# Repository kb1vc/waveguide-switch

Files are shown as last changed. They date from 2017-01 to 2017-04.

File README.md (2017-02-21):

# Description:

This is an OpenSCAD model for a positioner using a model airplane
servo to control a WR90 waveguide switch.

There are four major components in the SCAD file, each may be
printed separately.

The base holds the servo, a magnet to "capture" the positioning
slug, and two mounts for optical sensors that signal proper alignment
and positioning of the slug.

The slug connects to the shaft of the waveguide switch.  The slug
has two "vanes" that hold small magnets to latch the assembly into
the transmit or receive position.

The cap covers and protects the positioner and associated control
electronics.

For optimal performance, add a stripe of white or copper paint to
the "outside" edge of the slug vanes to provide a strong positive
reflection when the slug is in position.

---------
Arduino sketch
---------

The arduino sketch is written for the module described in the "module"
subdirectory. It is based on the Sparkfun Aruino Pro Mini. 

# License:
See the LICENSE.txt file for copyright and conditions for re-use.

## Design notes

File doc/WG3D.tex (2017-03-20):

\documentclass[12pt]{article}
% font size could be 10pt (default), 11pt or 12 pt
% paper size coulde be letterpaper (default), legalpaper, executivepaper,
% a4paper, a5paper or b5paper
% side coulde be oneside (default) or twoside 
% columns coulde be onecolumn (default) or twocolumn
% graphics coulde be final (default) or draft 
%
% titlepage coulde be notitlepage (default) or titlepage which 
% makes an extra page for title 
% 
% paper alignment coulde be portrait (default) or landscape 
%
% equations coulde be 
%   default number of the equation on the rigth and equation centered 
%   leqno number on the left and equation centered 
%   fleqn number on the right and  equation on the left side
%
\usepackage{graphicx}
\usepackage{geometry}
\usepackage{epigraph}
\usepackage{url}
\usepackage{fancybox}
\usepackage{textpos}
\usepackage{indentfirst}
\usepackage{rotating}
\usepackage{pdflscape}
\usepackage{listings}
\usepackage{tcolorbox}
\definecolor{light-gray}{gray}{0.95}
\usepackage{courier}
\usepackage{appendix}
\lstset{basicstyle=\footnotesize\ttfamily,breaklines=true,numbers=left}
%\usepackage{parskip}
%\setlength{\parskip}{\medskipamount}
\makeatletter
\newcommand{\@minipagerestore}{\setlength{\parskip}{\medskipamount}
\setlength{\parindent}{17pt}}
  \makeatother

\title{Reclaiming a Waveguide Switch -- An Adventure In 3D Printing}
\author{Matt Reilly  \\
	kb1vc \\
	}

\date{\today} 
% \date{\today} date coulde be today 
% \date{25.12.00} or be a certain date
% \date{ } or there is no date 
\begin{document}
% Hint: \title{what ever}, \author{who care} and \date{when ever} could stand 
% before or after the \begin{document} command 
% BUT the \maketitle command MUST come AFTER the \begin{document} command! 
\maketitle

\begin{abstract}
  A simple and somewhat reliable 3D printer can now be had for about \$200.
  While such a printer can help create new widgets and interesting objects, 
  it also affords an opportunity to refurbish or even reclaim equipment that
  may be lying around the shop in need of a hard-to-get part. This is the
  story of one such project that replaced a burned out actuator with a
  R/C model airplane servo and an Arduino controller.  All for 
  less than the cost of a replacement unit on eBay.
\end{abstract}

\setlength{\epigraphwidth}{0.8\textwidth}
\epigraph{[Engineering] is the art of doing that well with one dollar,
  which any bungler can do with two after a fashion.}{Arthur M. Wellington \\
  ``The Economic Theory of \\
  the Location of Railways''}

%\tableofcontents % create a table of contens 

\section{Introduction}

Most engineers read Mr. Wellington's dictum with great pride
that their training has placed them above the run-of-the-mill bungler.
I know that I do.
When it comes to mechanical engineering, however, I am a bungler.
In this case Wellington provides encouragement: it {\em may} be possible
to do what an expert can do for just twice the cost!

And so began my adventures in 3D printing.

\begin{figure}[htb]
  \centering
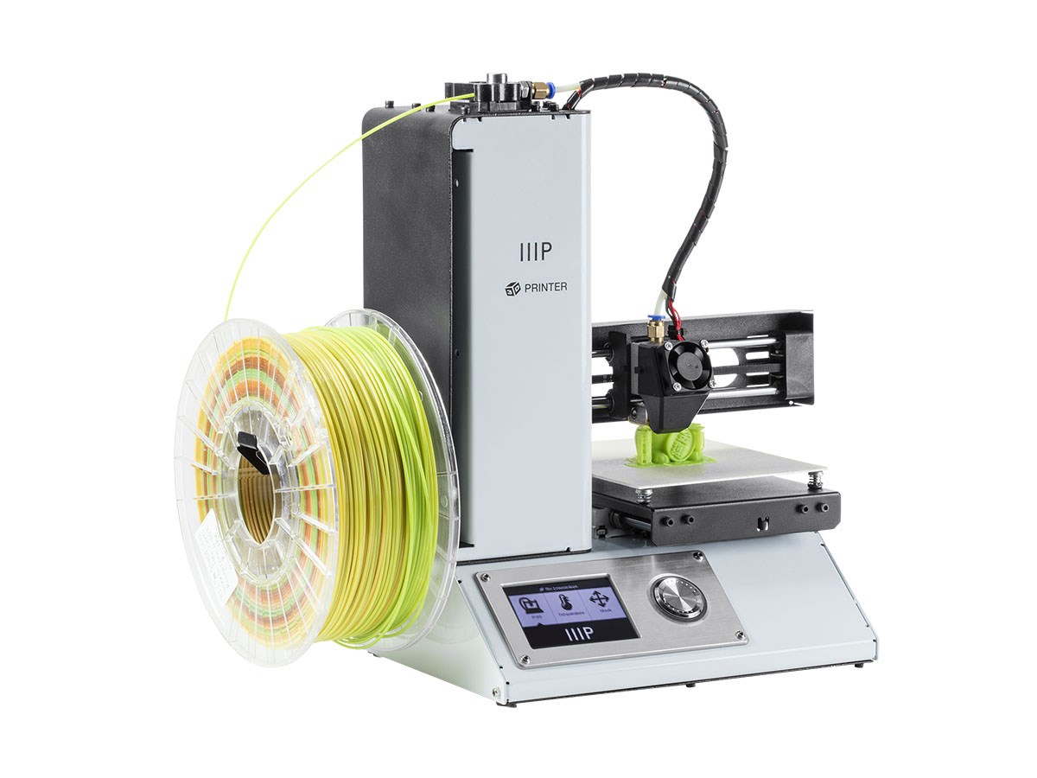
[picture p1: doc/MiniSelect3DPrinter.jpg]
  
  \caption{\label{f_printer}The Monoprice Mini Select 3D Printer}
\end{figure}

\section{Starting Simple}

This article is about reclaiming a WR75 waveguide switch by adapting
a common hobby airplane servo to function as the positioner. It comprises
a set of plastic parts to couple the servo to the waveguide slug,
and an Arduino controller.

But before we dive in to the construction of the waveguide switch positioner,
it may help to look at a much simpler 3D printing project.

Quite a while back, I bought an HP6289A DC power supply at a hamfest.
It was a real find, but at some point in its checkered past it had
been dropped on its face.  The fall shattered the two fine adjustment
knobs.  These were concentric with the coarse adjustment knobs on two
shafts: one for voltage and the second for current.  For years, the
absence of the knobs was no great annoyance. But one night I decided
that making replacements might be a short and simple project.

In the old days, I'd have scavenged in the scrap box for a nylon rod
or perhaps even an aluminum bar, mounted it in the lathe, turned it down,
bored out the hole for the shaft, tracked a few pieces of swarf while
passing through the living room, found that it didn't quite fit, tried
again... In total, I'd have spent a happy hour or two all together from
looking for bar stock, to vacuuming swarf out of the carpet.

This kind of project really points out the virtues of an inexpensive
3D printer.  No great precision is needed, and the cost of a mistake
is a small amount of material and time waiting for the
printer to finish.\footnote{The knobs were very small and simple. They
  took about 15 minutes to print. Typical
  print times for most interesting components can range from one to
  eight hours.}
It took two tries to get the design right. Had I
been paying attention, it could have been right the first time.
But having the printer in the shack
meant that I got through two iterations in less than an hour.
And no metal waste got stuck in the carpet. 

\begin{figure}[tb]
  \centering
  
  \caption{\label{f_3d_process}Printing in 3D from Idea to Widget}
\end{figure}

Figure \ref{f_3d_process} shows the path to a printed widget.  The
process starts with an idea which is reduced to a 3D model using
OpenSCAD to produce a stereo-lithography (STL) file.  The STL file
describes the object as a set of surfaces that bound a solid volume.
This is converted into instructions that move a 3D printer's extruder
and deposit the hot filament into the desired shape. The conversion
program is called a ``slicer'' because it converts the solid model
into a series of two dimensional planes that are deposited in layers
by the extruder.  The printer for this project is a Monoprice Mini
Select from \url{https://www.monoprice.com/} shown in Figure
\ref{f_printer}.The retail price is \$199. The quality of output from
the printer is variable, but compares favorably with much more
expensive printers. Though the manufacturers claim it can print in a
variety of materials, it works best with PLA, and not at all well with
ABS.

\begin{figure}[tb]
  %\caption*{About Materials}
\fbox{%
  \begin{minipage}{\textwidth}
\begin{tcolorbox}[colback=gray!35]
    \begin{center}
      {\bf About Materials}
    \end{center}
    ABS (Acrylonitrile Butadiene Styrene, for those keeping score at
    home) is the familiar plastic that shows up in instrument cases,
    helmets, canoes, and waste pipes.  It can be machined, and can
    even be given a glossy finish with exposure to acetone vapors.  It
    is, however, difficult to print on an economy-priced printer.

    PLA (Polylactic Acid) is most often found in disposable drinking
    cups.  It is often used where its potential for recycling is
    important. Some would claim that it is ``biodegradable'' as there
    are bacteria that eat it.  This has caused concern that
    widgets built with PLA might disintegrate while in use.  However,
    the process of breaking down PLA requires a fair amount of
    pressure and/or heat.  Relative durability for PLA can be assured
    by avoiding installations in compost heaps or animals.  Though my
    shack is something of a mess, it has not yet achieved the status
    of ``compost heap.''
    \end{tcolorbox}
\end{minipage}}
\end{figure}

Making the replacement knobs began with a model in OpenSCAD. OpenSCAD
scripts describe three dimensional things by building them
up from simple solids like cubes, spheres, cylinders, and cones.
Shapes can be added or subtracted, so that a simple knob can be
described as an outer cylinder minus an inner cylinder.  The inner
cylinder is the hole for the salvaged shaft collar. OpenSCAD allows the designer to
view an object on screen and to translate scripts into STL (stereo-lithography)
files for later processing. (The description language and the OpenSCAD
editor are described at \url{http://www.openscad.org/}.)

As this project aimed to replace the rather fancy HP original components,
the knobs had a bit of a taper to them, and a hole in the side for a
retaining screw. Figure \ref{f_openscad} is a screenshot of an OpenSCAD
session showing the knob. The model file is shown in Figure \ref{f_knob_list}.

\begin{figure}[htbp]
  \lstinputlisting{HP6289_inner.scad}
  \caption{\label{f_knob_list}OpenSCAD Model of Replacement Knob}
  \end{figure}

OpenSCAD scripts can follow many forms, but my own approach is to put
all of the important dimensions at the top of the file, and then
describe each feature of the object hierarchically.  For the knobs,
it was useful to describe the shaft diameter (line 2), 
the minimum wall thickness (line 3), the length of the knob (line 5),
the set screw (lines 6 and 7), and the depth of cut for the knurling (line 8).

The knob itself comprises a body, a hole for the shaft collar, a hole
for the setscrew, and the knurling.  These are all assembled in the
last module {\tt HP6289\_Inner}. The module is actually expanded in
lines 39 and 40.  OpenSCAD's default unit is the millimeter, but I
tend to measure in imperial units, so line 39 translates from inches
to mm.

\begin{figure}[tb]
  \centering
  \begin{minipage}[b]{0.4\textwidth}
    \centering
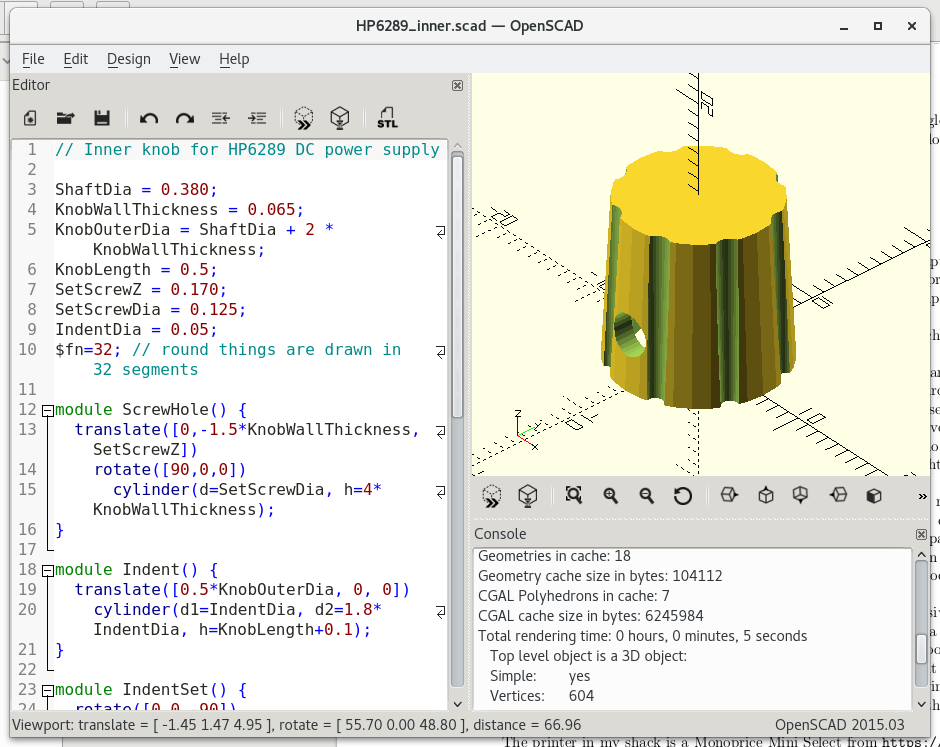
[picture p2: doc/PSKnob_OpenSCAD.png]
    
    \caption{\label{f_openscad}OpenSCAD session showing replacement knob}
  \end{minipage}\qquad
  \begin{minipage}[b]{0.4\textwidth}
    \centering
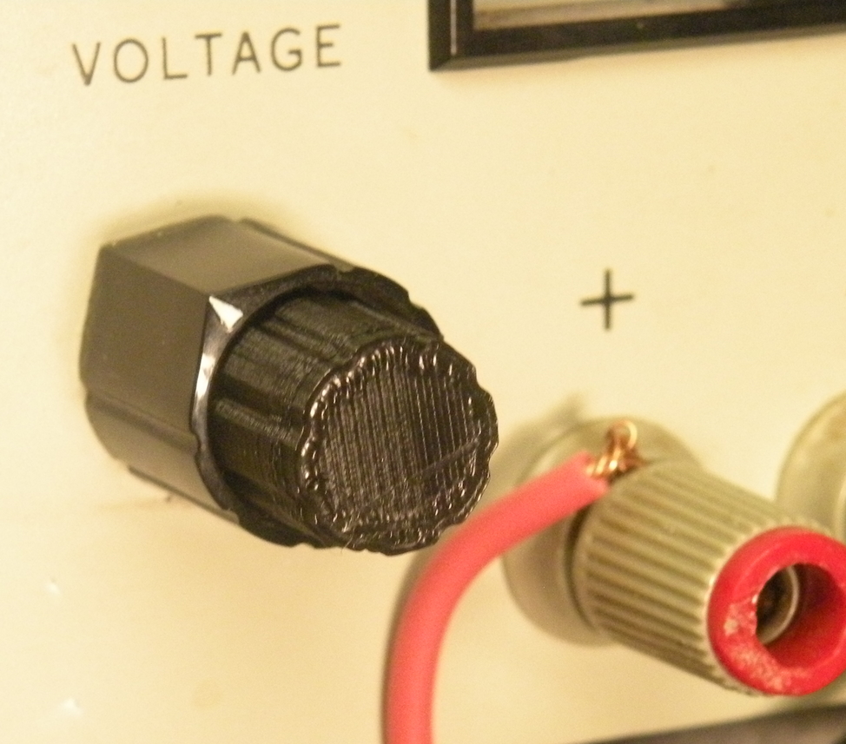
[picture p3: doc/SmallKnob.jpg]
    
    \caption{\label{f_knobs_on_box}Replacement power supply knob in its new home}
  \end{minipage}
\end{figure}

A pleasant evening of head-scratching and printing produced the two
knobs shown in Figure \ref{f_knobs_on_box}.  The result won't be
mistaken for original parts, but the power supply is a tool in a
workshop, not a museum display.

\section{The Waveguide Switch}

Years ago I bought a WR75 waveguide switch to use in a 10GHz transceiver.
The actuator was a pair of coils mounted to a shaft, and surrounded by
a pair of permanent magnets.  The shaft moved a slug inside the switch.
The switch functioned well for about ten years, but finally gasped its last
when one of the coils melted. (It appears that the microswitch that
handled the latching function may have gotten stuck.)

I disassembled the unit to complete the forensic investigation.  A short
examination convinced me that it was toast.  Rewinding the armature was
not all that appealing, and I'd recently acquired some good microwave relays,
so the broken shards sat on the shelf for a year or so, until I found the body
of the switch while looking for something else. The notion hit me that I
could replace the coil/magnet assembly with a R/C model airplane servo.
These were inexpensive and easy to control with an Arduino microcontroller
and a few lines of code.

Figure \ref{f_wg_switch_orig} shows a switch similar to the unit I started
with.\footnote{Thanks to Dudley Lab \url{http://www.dudleylab.com/surplus6.html} for the image.}  
The ``finished'' unit is shown in Figure \ref{f_wg_switch_new}. 

\begin{figure}[tb]
  \centering
  \begin{minipage}[b]{0.4\textwidth}
    \centering
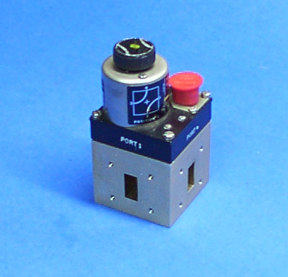
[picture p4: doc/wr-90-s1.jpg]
    
    \caption{\label{f_wg_switch_orig}Original switch (+/-)}  
  \end{minipage}
  \begin{minipage}[b]{0.4\textwidth}
    \centering
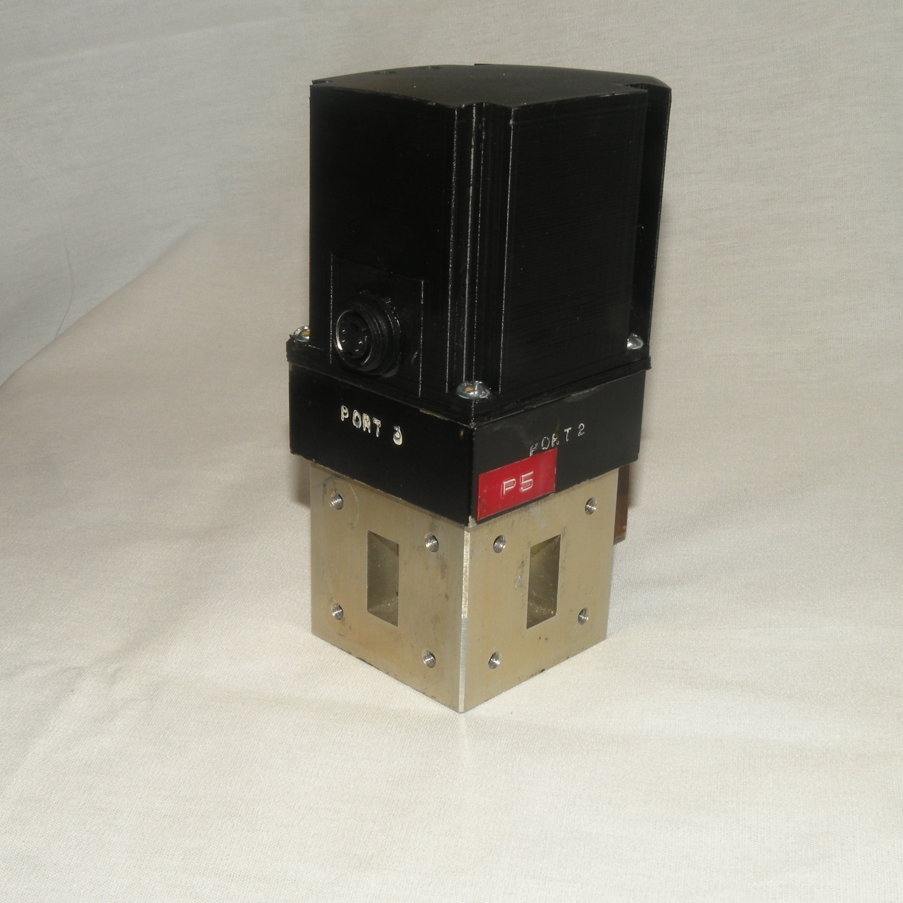
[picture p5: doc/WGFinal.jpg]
    
    \caption{\label{f_wg_switch_new}Reclaimed unit}      
  \end{minipage}
  \end{figure}

The trick was mating the servo to the keyed shaft of the waveguide switch,
and sensing the position of the switch.  A typical servo is not very
accurate. The control mechanism is a pulse train where the angular position
of the servo is more-or-less proportional to the pulse width.  The more-or-less
part meant that any positioning mechanism would need some kind of feedback
or other scheme to make sure the waveguide slug was aligned with the input
and output ports.

As an amateur bungler, it took a number of experiments before a
reasonably reliable method for positioning the slug was found. Figure
\ref{f_trial_and_error} shows 30 or so parts that were printed on the
way to a working design.  The total cost for all the material used in
the trials was less than \$10.

\begin{figure}[tb]
  \centering
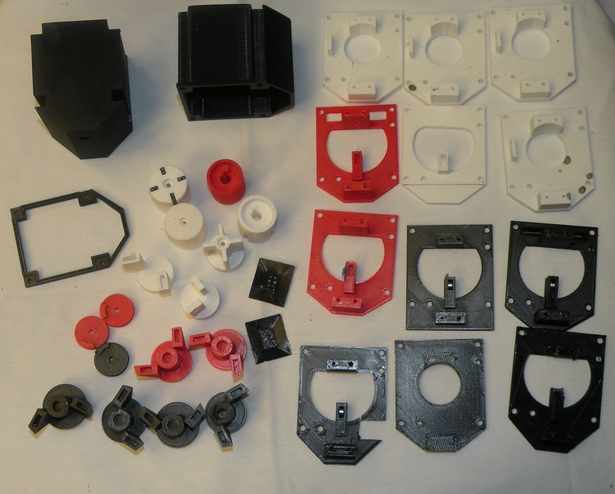
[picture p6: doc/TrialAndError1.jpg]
  
  \caption{\label{f_trial_and_error}Trial and Error Parts}
\end{figure}

\begin{figure}[thb]
\centering
    
    \caption{\label{f_expview}The Positioning Mechanism (minus the servo)}  
\end{figure}

Positional accuracy is established with a mechanical stop at each
position as shown by the assembly view in Figure \ref{f_expview}. The
metal slug in the waveguide switch itself is coupled to a positioner
(dark gray) that is pushed by the puck (white) into the RX or TX
position, and stopped by a protrusion on the base (red). Each vane in
the positioner has a pocket for a small 6mm rare earth magnet. These
are captured by a magnet in the pocket in the stop block on the
base. The servo needs only to push the positioner vane to the stop and
may then recede. The magnets hold the positioner (and the waveguide
slug) in place until the servo is commanded to switch modes.  As a
``fail-safe'' mechanism, the controller will not assert its TX\_EN
output line until an infra-red position sensor detects that the
positioner vane is in place against the stop block.  On deassertion of
the PTT line, the controller maintains the servo position against the
positioner until a similar IR sensor on the RX side detects that the
positioner is in place against the stop block on the RX side.

The servo is controlled with an Arduino Pro Mini (available from
Sparkfun at \url{https://www.sparkfun.com/products/11113}) on a module
that provides level translation and limited isolation for the PTT
input line and the TX\_EN output line. (See Appendix \ref{a_controller_module}
for the schematic.)

The OpenSCAD files, the schematic and PCB layout, and Arduino code are
all available for use under the ``BSD 2-clause Simplified License'' that
allows commercial use, modification, distribution, and private use.
The design package can be downloaded from github at \url{https://github.com/kb1vc/waveguide-switch}.

\section{Building the Switch}

It would be surprising if anyone actually built exactly this module,
as it will likely require some modification for each type of waveguide
switch.  Nevertheless, the assembly instructions are provided here to
serve as a starting point for others. Assembly directions are tedious
and make for lousy reading.  You've been warned. 

\subsection{The Arduino Controller}

The first version of the Arduino based controller assumed ground-to-actuate
input for the PTT switch that was routed directly to the microcontroller.
(See the schematic in Appendix \ref{a_controller_module}.)
This is a really bad idea, so revision B will have some protection on this
input to isolate the microcontroller from potentially damaging voltages on the
PTT line and to provide some RF decoupling.
The REV A modules are available from OSH Park at \url{https://oshpark.com/shared_projects/Da0N0VIn}.
REV B is ``in progress.''

Assembly of the controller is straightforward, though almost all the components
are surface-mounted. The Pro Mini is soldered to the module as a daughter card.
The Pro Mini is availble in both 3.3V and 5V versions.  This controller uses the
5V model, as this tends to be better suited to driving an RC servo.

Once assembled, the controlling sketch may be downloaded into the module using a
USB to serial adapter from Sparkfun. (\url{https://www.sparkfun.com/products/9716})

The sketch is found in the design package under {\tt ../arduino/TRSwitchSleep}
and its current version is shown in Appendix \ref{a_sketch}. 
This sketch senses changes on the PTT input and activates the servo.
The servo is driven to its limit until the IR sensors mounted on the base indicate
that the positioner vane is pushing against the stop block. 
The TX enable output line is asserted {\em only} after the IR sensor detects
that the positioner is in the TX position.  The TX enable line is deasserted
(floats) as soon as the microcontroller detects a rising edge on the PTT input.
The sketch places the microcontroller in sleep mode between switching events to
reduce RF noise caused by its internal (and rather dirty) oscillators. 

\subsection{The Mechanical Bits}

The 3D printed parts for the switch are all described in a single
OpenSCAD file.  However, most small 3D printers will need to print
the lid and base parts separately, as they take up a fair amount
of room on the printer's platform.
To print the components:
\begin{enumerate}
\setlength\itemsep{0em}
\item Use OpenSCAD to generate an STL file (called {\tt WGSwitch.stl}) from
  the {\tt WGSwitch.scad} source file.
\item Open the {\tt WGSwitch.stl} file in Cura
\item Click MB3 on the model and select ``Split object into parts.''
  This will separate the four parts.
\item Delete the lid and the  base.
\item Save the gcode file as {\tt WGSwitchSmall.gcode}.
\item Quit Cura, then repeat steps 2 and 3.
\item This time delete all the parts except the base.
\item Save the gcode file as {\tt WGSwitchBase.gcode}.
\item Quit Cura, then repeat steps 2 and 3.
\item Delete all the parts except the lid.
\item Flip the lid over so that its open part faces up.
\item Save the gcode file as {\tt WGSwitchLid.gcode}.
\item Copy each of the gcode files to your 3D printer.
\item For best results, print the all components in black.
  At a minimum, the positioner and the base must be printed
  in a color that does not reflect IR well.
  \end{enumerate}

It would be a very bad idea to make this your {\em first} 3D printing
experience, as every printer requires a little fiddling and some
occasional attention.  The typical 3D printer is not nearly as
reliable as a 2D inkjet printer.

\begin{figure}[tb]
  \centering
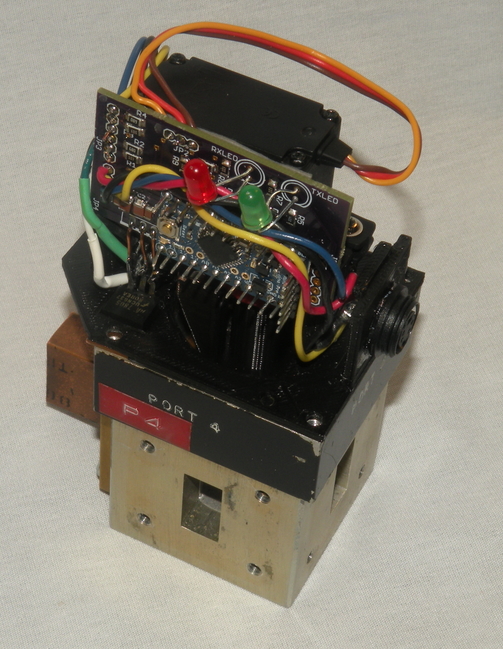
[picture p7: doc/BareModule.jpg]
  
  \caption{\label{f_naked_switch}The Controller, Servo, and Sensors}
\end{figure}

Once the parts have been printed, they should be ``tidied up'' with
a sharp knife here and there.  
The switch controller, {\em sans} lid, is shown in Figure \ref{f_naked_switch}.
Assembly is fairly straightforward.

\begin{enumerate}
\setlength\itemsep{0em}  
\item Mount the round puck on the shaft of the RC servo. Rotate the
  servo so that the shaft is at its midpoint position. Then align
  the key on the puck so that it is closest to the midpoint of the
  two mounting holes nearest the servo's shaft.
\item Mount the positioner onto the waveguide slug.
\item Insert two of the rare-earth magnets into the slots in
  the positioner, making sure the magnets are both facing with
  their poles in the same direction.
\item Place the base onto the waveguide switch body, lining up
  the locator and screw holes. Insert the LM7805 voltage regulator
  into the slot in the base. Ensure that the positioner vanes
  straddle the stop block in the base. Fasten the base to the
  switch body with four screws.
\item Insert a magnet into the slot in the base, making sure
  it is oriented so that it attracts each of the vanes in turn.
\item Glue the two IR proximity sensors into the base using
  a two-part epoxy.
\item Wire the IR sensors, the servo, and a 4 pin DIN connector
  to the controller module.
\item Fasten the controller to the side of the servo with
  double sided tape.
\item Paint a small reflective stripe on each of the vanes of the
  positioner, as shown in Figure \ref{f_positioner_stripe}.
  These will improve the reflectivity of the block. 
\item Glue the 4 pin DIN socket into the hole at one end
  of the base.
  \item Carefully stuff all that into the lid. 
  \end{enumerate}

\begin{figure}[tb]
  \centering
  
  \caption{\label{f_positioner_stripe}Reflective Stripes on the Positioner Vanes}
\end{figure}

\begin{figure}[tb]
  %\caption*{About Materials}
\fbox{%
  \begin{minipage}{1.1\textwidth}
\begin{tcolorbox}[colback=gray!35]
    \begin{center}
      {\bf Drawing in 3D}
    \end{center}
There are lots of choices for preparing 3D models
for printing.  I prefer to use open source software.
Of the open source choices, I've used two:  FreeCAD
and OpenSCAD. 

FreeCAD is an open source alternative to the traditional
3D CAD suites like SolidWorks.  The interface and
the behavior will be familiar to users of the commercial
tools.  It provides a rich set of ``workbenches'' that
assist in creating parts, assemblies, and 2D drawings.
It is under active development, and has a support community.

OpenSCAD uses a script based approach to create constructive
solid geometry  models.  It is extremely powerful, and capable
of describing just about any physically realizable shape.

I started in 3D printing as a FreeCAD user.  It allowed me to
build boxes, knobs, and robot parts. However, I found that making
changes to a design was hit-and-miss.  The data structures that
FreeCAD used often made it impossible to move a hole a few mils,
or change the angle between two slabs.  After a particularly
aggravating episode where  several hours of work had to be
discarded because a hole was in the wrong place, I abandoned FreeCAD.

OpenSCAD encourages a cut-and-try approach that allows
easy modification.  The learning curve can be quite steep for
users who have never written a program before, but not insurmountable.

A third option offers a graphical approach to constructive solid geometry. 
Many elementary schools are using Tinkercad (\url{https://www.tinkercad.com})
to introduce students to 3D printing. Tinkercad runs in a web browser, but
allows the user to create models and download them for printing on a
3D printer. 
    \end{tcolorbox}
\end{minipage}}
\end{figure}

\clearpage
\section{Final Thoughts}

The arrival on the market of
an inexpensive 3D printer, and the well established Arduino
culture have given hams a new set of tools.  Experiments are
cheap and take far less time than traditional machine-shop
ventures. The project described here was done over a few
widely spaced weekends, despite the dozens of experiments
and refinements along the way. 

Building it was fun. The trial-and-error-and-error approach
took advantage of the low cost of each print.
The CAD tools allowed progressive refinement.
The minimal investment for each design iteration meant
that ``throw it out and start over'' was always an option.
The printer produced a usable device. And the
tools are available to any bungler.

\clearpage

\begin{appendices}

\section{\label{a_sketch}The Controller Arduino Sketch}
\lstinputlisting{../arduino/TRSwitchSleep/TRSwitchSleep.ino}

\clearpage
\newgeometry{top=1cm,bottom=1cm,left=1cm,right=1cm}
\section{\label{a_controller_module}The Servo Controller Module}
\begin{figure}[h] 
  \centering
  
\end{figure} 

%%\newpage
%%\newgeometry{top=1cm,bottom=1cm,left=1cm,right=1cm}
%%\section{\label{a_controller_mdoule}The Servo Controller Module}
%%
%%\begin{landscape}
%%\includegraphics[width=0.6\linewidth,keepaspectratio]{WGSwitchSchematic.pdf}
%%  \end{landscape}
%%\restoregeometry

\end{appendices}
\end{document}

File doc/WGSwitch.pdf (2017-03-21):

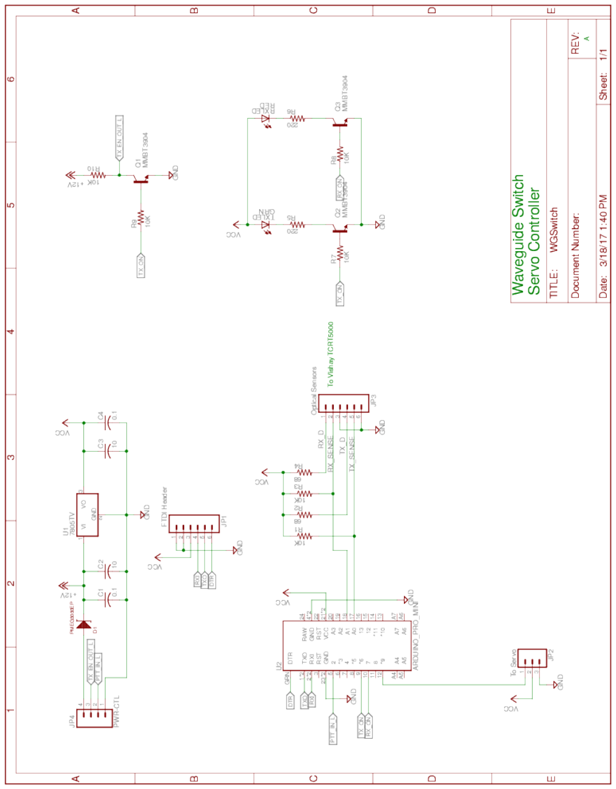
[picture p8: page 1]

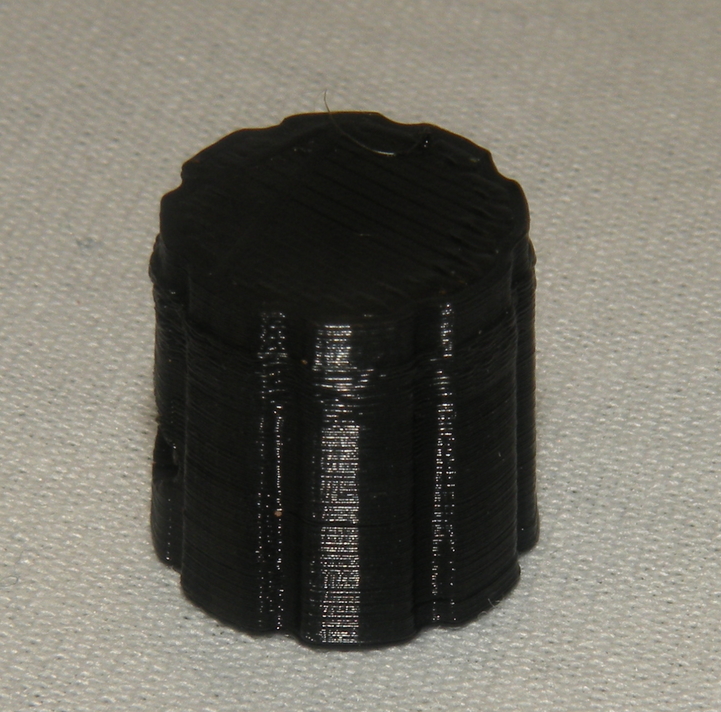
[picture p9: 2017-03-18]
doc/SmallKnobAlone.jpg

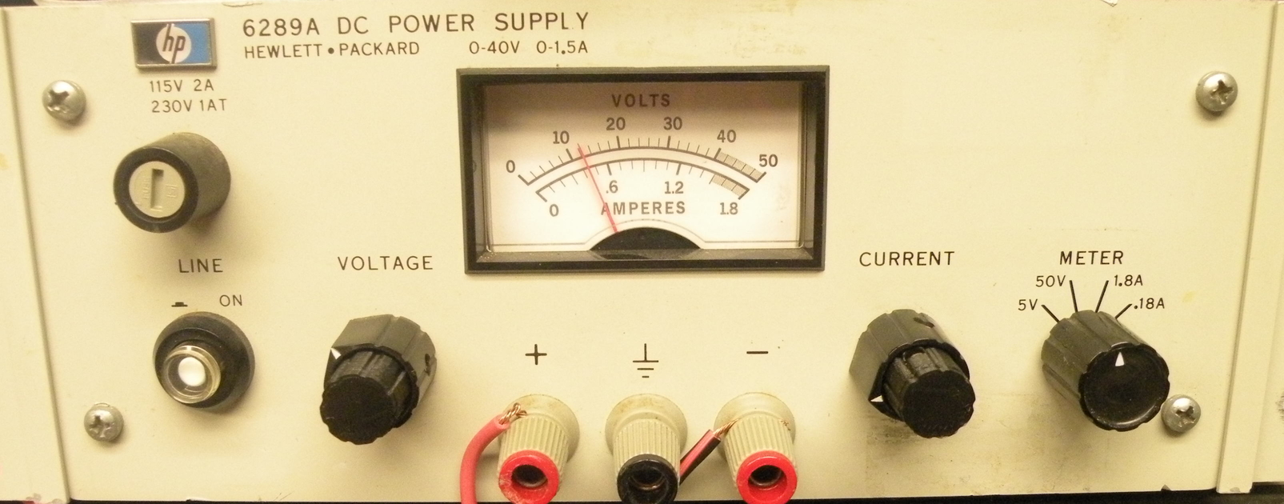
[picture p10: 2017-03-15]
doc/PSKnobs.jpg

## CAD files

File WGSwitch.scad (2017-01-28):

/*
  WGSwitch.scad
 
  Author: radiogeek381@gmail.com

 A replacement for the electro-magnetic actuated servos on a
 WR90 waveguide switch.  This uses a standard model R/C servo
 to move the slug, and permanent magnets to hold the slug in place.
*/ 
/*
Copyright (c) 2016, Matthew H. Reilly (kb1vc)
All rights reserved.

Redistribution and use in source and binary forms, with or without
modification, are permitted provided that the following conditions are
met:

    Redistributions of source code must retain the above copyright
    notice, this list of conditions and the following disclaimer.
    Redistributions in binary form must reproduce the above copyright
    notice, this list of conditions and the following disclaimer in
    the documentation and/or other materials provided with the
    distribution.

THIS SOFTWARE IS PROVIDED BY THE COPYRIGHT HOLDERS AND CONTRIBUTORS
"AS IS" AND ANY EXPRESS OR IMPLIED WARRANTIES, INCLUDING, BUT NOT
LIMITED TO, THE IMPLIED WARRANTIES OF MERCHANTABILITY AND FITNESS FOR
A PARTICULAR PURPOSE ARE DISCLAIMED. IN NO EVENT SHALL THE COPYRIGHT
HOLDER OR CONTRIBUTORS BE LIABLE FOR ANY DIRECT, INDIRECT, INCIDENTAL,
SPECIAL, EXEMPLARY, OR CONSEQUENTIAL DAMAGES (INCLUDING, BUT NOT
LIMITED TO, PROCUREMENT OF SUBSTITUTE GOODS OR SERVICES; LOSS OF USE,
DATA, OR PROFITS; OR BUSINESS INTERRUPTION) HOWEVER CAUSED AND ON ANY
THEORY OF LIABILITY, WHETHER IN CONTRACT, STRICT LIABILITY, OR TORT
(INCLUDING NEGLIGENCE OR OTHERWISE) ARISING IN ANY WAY OUT OF THE USE
OF THIS SOFTWARE, EVEN IF ADVISED OF THE POSSIBILITY OF SUCH DAMAGE.
*/

// All dimensions are in inches -- scaling to mm is at the end.

$fn=32;

// the base plate that is screwed to the top
// of the waveguide switch
BaseX = 2.6;
// for reasons I can't recall BaseX is involved in the positioning of
// the slug's magnet boxes.. go figure.
BaseXOuter = 2.8;
BaseY = 2.1;
BaseZ = 0.1;

FrameRailWidth = 0.15;

MountX = 0.22;
MountY = 0.7;
MountZ = 0.950;
// was 0.415
MountPos = [ [0.380, 0.5 * (BaseY - MountY), 0], [2.31, 0.5 * (BaseY - MountY), 0] ];

// My printer undersizes round Z axis holes by about this much.
HoleCorrection = 0.013;
// and it undersizes z axis pegs by about this much.
PegCorrection = 0.005; 

CenterHoleDia = 1.6; 
// the base is really a square with an extension off the end of the right edge.
CenterHolePos = [0.5*BaseY - 0.035, 0.5*BaseY, 0]; 

ServoCenterOffsetX = 0.540; 
ServoCenterYSpace = 0.4;
ServoCenterXSpace = 1.9; 
ServoMountHoleDia = 0.08; 
ServoMountHoleZ = MountZ * 2;
ServoMountLLHole = CenterHolePos - [ServoCenterOffsetX, 0.5 * ServoCenterYSpace, 0];
ServoMountULHole = ServoMountLLHole + [0, ServoCenterYSpace, 0];
ServoMountURHole = ServoMountULHole + [ServoCenterXSpace, 0, 0];
ServoMountLRHole = ServoMountLLHole + [ServoCenterXSpace, 0, 0];
ServoMountHolesPos = [ServoMountLLHole, ServoMountULHole, ServoMountURHole, ServoMountLRHole ];

ScrewHoleDia = 0.135 + HoleCorrection; 
LocatorHoleDia = 0.135 + HoleCorrection;

ScrewSquareDim = 1.845;
ScrewHoleLLPos = [0.055 + 0.5*ScrewHoleDia, 0.055 + 0.5 * ScrewHoleDia, 0]; 
ScrewHoleULPos = ScrewHoleLLPos + [0, ScrewSquareDim, 0];
ScrewHoleURPos = ScrewHoleULPos + [ScrewSquareDim, 0, 0];
ScrewHoleLRPos = ScrewHoleLLPos + [ScrewSquareDim, 0, 0];
ScrewHolesPos = [ScrewHoleLLPos, ScrewHoleULPos, ScrewHoleURPos, ScrewHoleLRPos];


LocatorULPos = ScrewHoleULPos + [0.427, 0, 0];
LocatorLRPos = ScrewHoleLRPos + [0, 0.427, 0];
LocatorHolesPos = [LocatorULPos, LocatorLRPos];

StopBoxX = 0.75;
StopBoxY = 0.25;
StopBoxZ = 0.3 + BaseZ;
SlotX = 0.28; 
StopBoxOffsetX = 1.35;
StopBoxOffsetY = 0.5 * (BaseY - StopBoxY);
BoxWallWidth = 0.065;
// This is the amount of "slack" we want between stop faces
// 10 mils for now
BoxRelief = 0.01;

// this is the height of the cap above the bottom of the switch well. 
CapOffsetZ = 0.7; 

// Now the slug parts
SlugInnerDia = 0.75 + HoleCorrection;
SlugWallThickness = 0.065;
SlugOuterDia = SlugInnerDia + 2 * SlugWallThickness;
SlugTopDia = CenterHoleDia; // - 0.05;
SlugInnerDepth = 0.125;
SlugZ = CapOffsetZ + StopBoxZ - 0.05; // give a little relief to avoid fouling the puck
SlugKeyLength = 0.125;
SlugKeyDia = 0.18 + PegCorrection;

// This needs to accommodate a hole for the servo axis
BearingOuterDia = 0.5;
BearingInnerDia = 0.25;
BearingHoleDepth = 0.3;

// These are the dimensions for the servo puck
// that pushes the slug's wings
PuckDiameter = 0.82;
PuckHeight = 0.215;
PuckKeyHeight = 0.4; // added some height to get a good hit on the slug
PuckKeyAngle = 40;  // 60 requires some finesse -- running stop to stop will bind.
PuckScrewHole = 0.125;
PuckSplineHole = 0.245;
PuckSplineHoleDepth = 0.14;
PuckOffsetZ = SlugZ + PuckHeight + 0.075;

CaseWallThickness = 0.1; 
LidInsideHeight = 2.1;
LidOutsideHeight = LidInsideHeight + CaseWallThickness;
LidScrewReliefDia = 0.25;
LidScrewReliefBox = 0.3;

// given a list of positions, subtract each of the objects
// from the first object. 
module DrillZ() {
    difference() {
        children(0);
	    for(i = [1:$children-1]) {
	        // Make the hole a little bigger in the Z dim, then
	        // shift it down by half that amount
	        scale([1,1,2.01])
	            translate([0,0,-0.001])
  		        children(i);
	    }
    }
}

module ZPost(dia, depth, pos) {
    translate(pos)
        translate([0,0,0.01])
            rotate([0, 0, 90])
	        cylinder(d=dia, h=depth+0.02, center=true);
}

DummyServoZBump = 0.26;
module DummyServo()
{
    cube([ServoCenterXSpace, ServoCenterYSpace, 0.1]);
    translate([ServoCenterXSpace*0.25, 0, -(DummyServoZBump)])
        cube([ServoCenterXSpace*0.5, ServoCenterYSpace, DummyServoZBump]);
}

module WGBase() {
    union() {
        cube([BaseXOuter,BaseY,BaseZ]);
        for(p = MountPos) {
            translate(p) 
                cube([MountX, MountY, MountZ]);
        }
    }
    
}

module CenterHole() {
    xd = MountPos[0].x;
    difference() {
        ZPost(dia=CenterHoleDia, depth=BaseZ, pos=CenterHolePos);
        translate([0,0,-0.05])
            cube([MountPos[0].x + MountX, BaseY, 1.4 * BaseZ]);
    }
}

module StopBox() {
    translate([StopBoxOffsetX, StopBoxOffsetY, 0])
        difference() {
            cube([StopBoxX, StopBoxY, StopBoxZ]);
	    translate([BoxWallWidth, BoxWallWidth, StopBoxZ - SlotX + 0.01])
	        cube([SlotX, StopBoxY - BoxWallWidth * 2, SlotX]);
	}
}

module FrameBoxHoles() {
  slot0x = MountPos[0].x - FrameRailWidth;
  slot0ypos = ScrewHoleLLPos.y * 2;
  slot0y = BaseY - 2 * slot0ypos; 
  //translate([FrameRailWidth, slot0ypos,-0.01]) {
  //    cube([MountPos[0].x - FrameRailWidth, slot0y, 2 * BaseZ]);
  //}
  translate([0,0,-0.01]) {
      triX = ScrewHoleLRPos.x + ScrewHoleDia;
      triY = 0.5 * (BaseY - MountY);
      linear_extrude(height=BaseZ*2) {
          polygon(points = [ [triX, -0.01], [BaseXOuter + 0.01, 0], [BaseXOuter + 0.01, triY] ] );
          polygon(points = [ [triX, BaseY + 0.01], [BaseXOuter + 0.01, BaseY + 0.01], [BaseXOuter + 0.01, BaseY - triY] ] );
      }

  }
}


module WGCap() {
    DrillZ() {
        WGBase();
        for(p = ScrewHolesPos) {
            ZPost(dia=ScrewHoleDia, depth=BaseZ, pos=p);
        }
        for(p = LocatorHolesPos) {
            ZPost(dia=LocatorHoleDia, depth=BaseZ, pos=p);
        }
	for(p = ServoMountHolesPos) {
	    ZPost(dia=ServoMountHoleDia, depth=ServoMountHoleZ, pos=p);
	}
	FrameBoxHoles();
        CenterHole();
    }
    StopBox();
}

module SlugBody() {
    cut_offset_z = SlugInnerDepth + SlugWallThickness;
    difference() {
        translate([0, 0, 0.5 * SlugZ])
            cylinder(d1=SlugOuterDia, d2=SlugTopDia, h = SlugZ - 0.01, center = true);
	// cut the hole in the bottom
	translate([0,0,0.5 * SlugInnerDepth])
	    cylinder(d=SlugInnerDia, h = SlugInnerDepth+0.05, center=true);
	// cut the Corner betwen the two stops
	translate([-0.5 * StopBoxY - BoxRelief, -0.5 * StopBoxY - BoxRelief, cut_offset_z])
	   cube([SlugTopDia, SlugTopDia, SlugZ]);
	translate([-0.5*SlugTopDia, -1.5 * StopBoxY - SlugTopDia, cut_offset_z])
	    cube([SlugTopDia, SlugTopDia, SlugZ]);
	translate([-1.5 * StopBoxY - SlugTopDia, -0.5 * SlugTopDia, cut_offset_z])
	   cube([SlugTopDia, SlugTopDia, SlugZ]);
	// now cut out the "back" of each wing to keep it from fouling the mount
	translate([0.15 * SlugTopDia, 0.15 * SlugTopDia, cut_offset_z])
	   rotate([0,0,180])
	       cube([SlugTopDia, SlugTopDia, SlugZ]);
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

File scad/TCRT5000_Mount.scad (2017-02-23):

/*
	TCRT5000_Mount

	Author: radiogeek381@gmail.com

	A slab with holes arranged to fit the
	TCRT5000 optical sensor from Vishay.
	http://www.vishay.com/docs/83760/tcrt5000.pdf
*/

// dimensions in mm -- use TCRT5000_Mount_in() for designs
// that scale to mm at the last stage.
//
// Or use TCRT5000_Mount_mm() to get a scaled to mm version.

TCRT5000_Z = 1.55;
TCRT5000_Y = 5.8;


BaseX = 10.2;
BaseY = TCRT5000_Y;
BaseZ = TCRT5000_Z;

CenterX = 4.65;
CenterY = 2.45;

MountHolePos = [ [ CenterX, CenterY + 1.9, 0], [ CenterX, CenterY - 1.9, 0 ] ];
    

LeadHoleLX = CenterX - 2.75;
LeadHoleRX = CenterX + 2.75; 
LeadHoleLY = CenterY - 1.27;
LeadHoleUY = CenterY + 1.27; 
LeadHolePos = [ [LeadHoleLX, LeadHoleLY, 0], [LeadHoleLX, LeadHoleUY, 0], [LeadHoleRX, LeadHoleLY, 0], [LeadHoleRX, LeadHoleUY, 0] ];
SlabOffsetX = 1.5;
SlabOffsetY = 1.5; 

HoleDepth = BaseZ * 4; 


function TCRT5000_Z_mm() = TCRT5000_Z; 
function TCRT5000_Z_in() = TCRT5000_Z / 25.4;
function TCRT5000_Y_mm() = TCRT5000_Y;
function TCRT5000_Y_in() = (TCRT5000_Y + 1.5*SlabOffsetY) / 25.4;

$fn=32;
module TCRT5000_Mount_mm() {

    translate([SlabOffsetX, SlabOffsetY, -BaseZ]) difference() {
        translate([-SlabOffsetX, -SlabOffsetY, 0])
            cube([BaseX + SlabOffsetX, BaseY + 1.5*SlabOffsetY, BaseZ]);
	// datum hole
        translate([0, 0, -0.1]) {
   	    cylinder(d1 = 1.5, h = HoleDepth, center=true);
	    for(p = LeadHolePos) {
	        translate(p) cylinder(d1 = 1.5, h = HoleDepth, center=true);
	    }
	    for(p = MountHolePos) {
	        translate(p) cylinder(d1 = 2.5, h = HoleDepth, center=true);
	    }
	}
    }
}


module TCRT5000_Mount_in() {
    sf = 1.0 / 25.4;
    scale([sf, sf, sf]) TCRT5000_Mount_mm();
}

// test

TCRT5000_Mount_mm();

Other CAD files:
scad/WGSwitch.scad
doc/ExplodedView.scad
doc/HP6289_inner.scad

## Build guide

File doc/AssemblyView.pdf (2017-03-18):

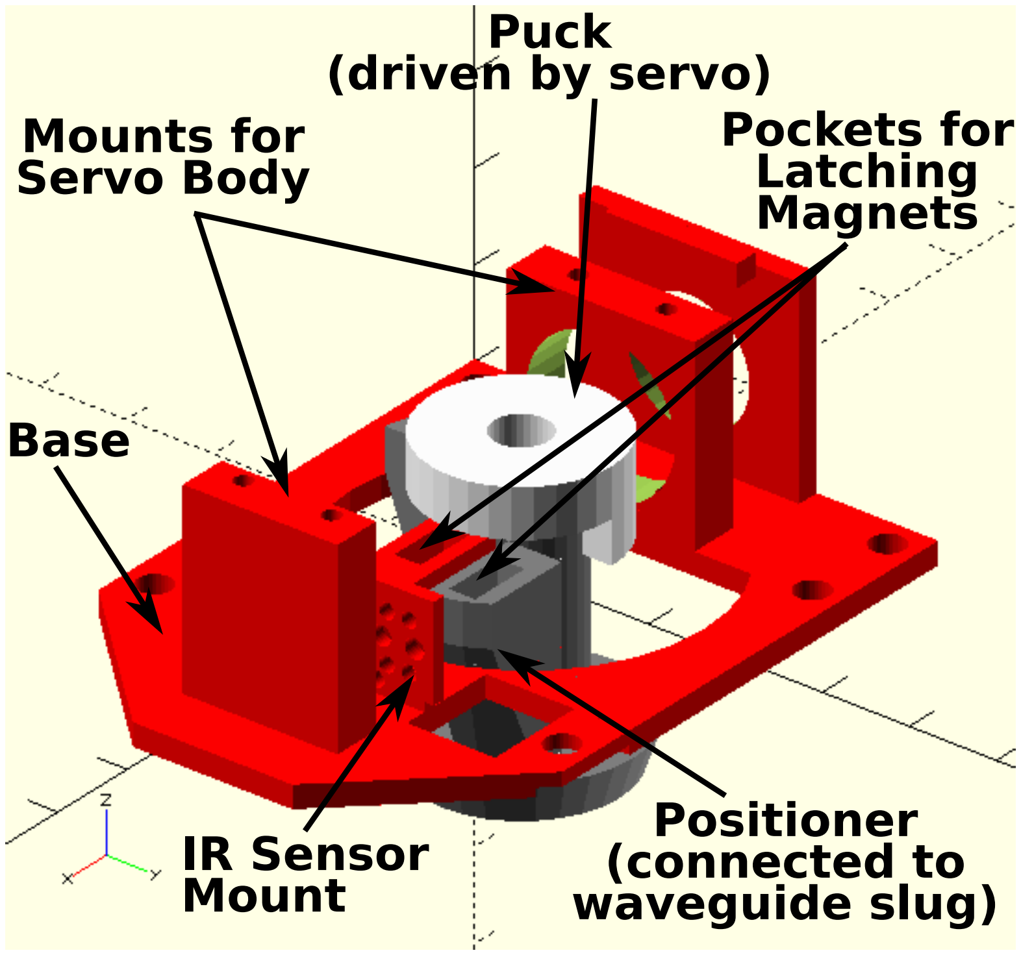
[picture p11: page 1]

Puck
(driven by servo)

Base

Mounts for
Servo Body

Positioner
(connected to
waveguide slug)

Pockets for
Latching
Magnets

IR Sensor
Mount

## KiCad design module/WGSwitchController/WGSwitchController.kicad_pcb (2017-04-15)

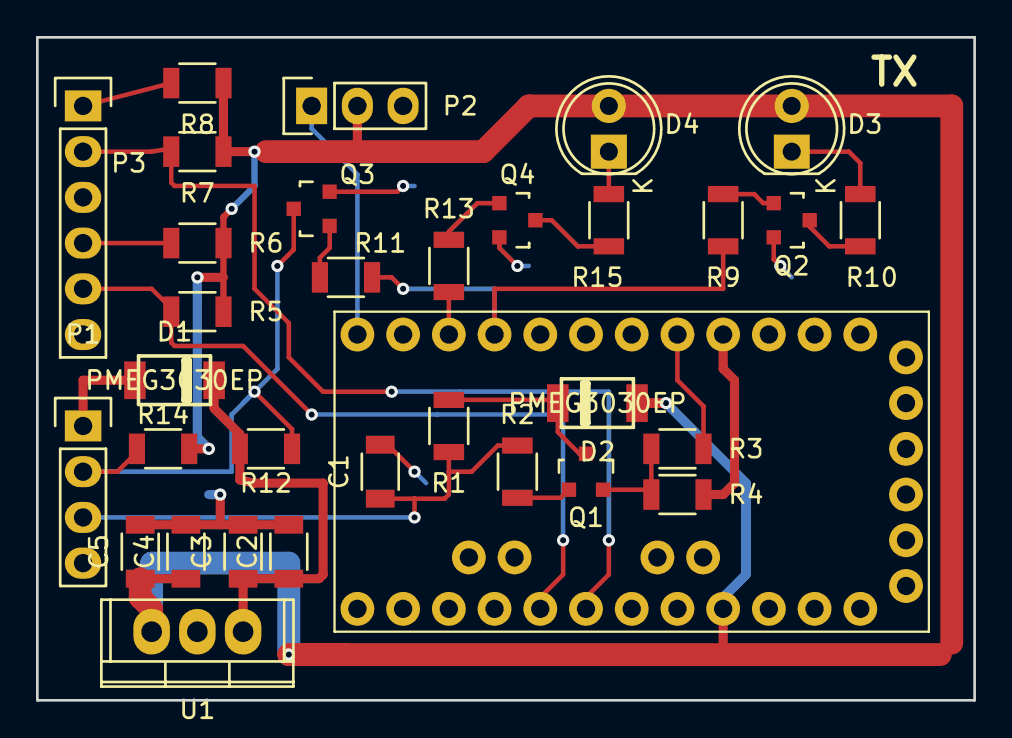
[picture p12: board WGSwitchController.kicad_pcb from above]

Board: 2 copper layers, 52.1 x 36.8 mm, 33 parts (0 on the bottom side), 24 nets.

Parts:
C1: C; C_1206
C2, C4: 0.1; C_1206
C3, C5: 10; C_1206
D1, D2: PMEG3030EP; SOD-128
D3: GRN LED; LED-5MM
D4: RED LED; LED-5MM
M1: ARDUINO_PRO_MINI
P1: CONN_01X04; Pin_Header_Straight_1x04
P2: CONN_01X03; Pin_Header_Straight_1x03
P3: CONN_01X06; Pin_Header_Straight_1x06
Q1: MMBT3906; SOT-23
Q2, Q3, Q4: MMBT3904; SOT-23
R1, R2, R3, R4, R5, R7, R9, R11, R12, R13, R14: 10K; R_1206
R6, R8: 68; R_1206
R10, R15: 220; R_1206
U1: LM7805CT; TO-220

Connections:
+5V: C4.1, C5.1, D2.2, D3.2, D4.2, M1.21, P2.2, R5.1, R6.1, R7.1, R8.1, R14.1, U1.3
+12V: C2.1, C3.1, D1.1, R12.1, U1.1
GND: C1.2, C2.2, C3.2, C4.2, C5.2, M1.4, M1.23, P1.4, P2.3, P3.3, P3.6, Q2.2, Q3.2, Q4.2, R3.2, U1.2
unnamed: D1.2, P1.1
unnamed: D2.1, Q1.3, R1.2
unnamed: D3.1, R10.1
unnamed: D4.1, R15.1
unnamed: M1.12, P2.1
unnamed: P3.1, R8.2
unnamed: P3.4, R6.2
unnamed: Q1.1, R2.1
unnamed: Q1.2, R3.1, R4.2
unnamed: Q2.1, R9.1
unnamed: Q2.3, R10.2
unnamed: Q3.1, R11.1
unnamed: Q4.1, R13.1
unnamed: Q4.3, R15.2
PTT_IN_RAW_L: C1.1, P1.3, R1.1, R2.2
RX_ON: M1.10, R13.2
RX_SENSE: M1.18, P3.2, R7.2
TX_EN_IN_H: M1.5, R4.1
TX_EN_OUT_L: P1.2, Q3.3, R12.2, R14.2
TX_ON: M1.9, R9.2, R11.2
TX_SENSE: M1.17, P3.5, R5.2

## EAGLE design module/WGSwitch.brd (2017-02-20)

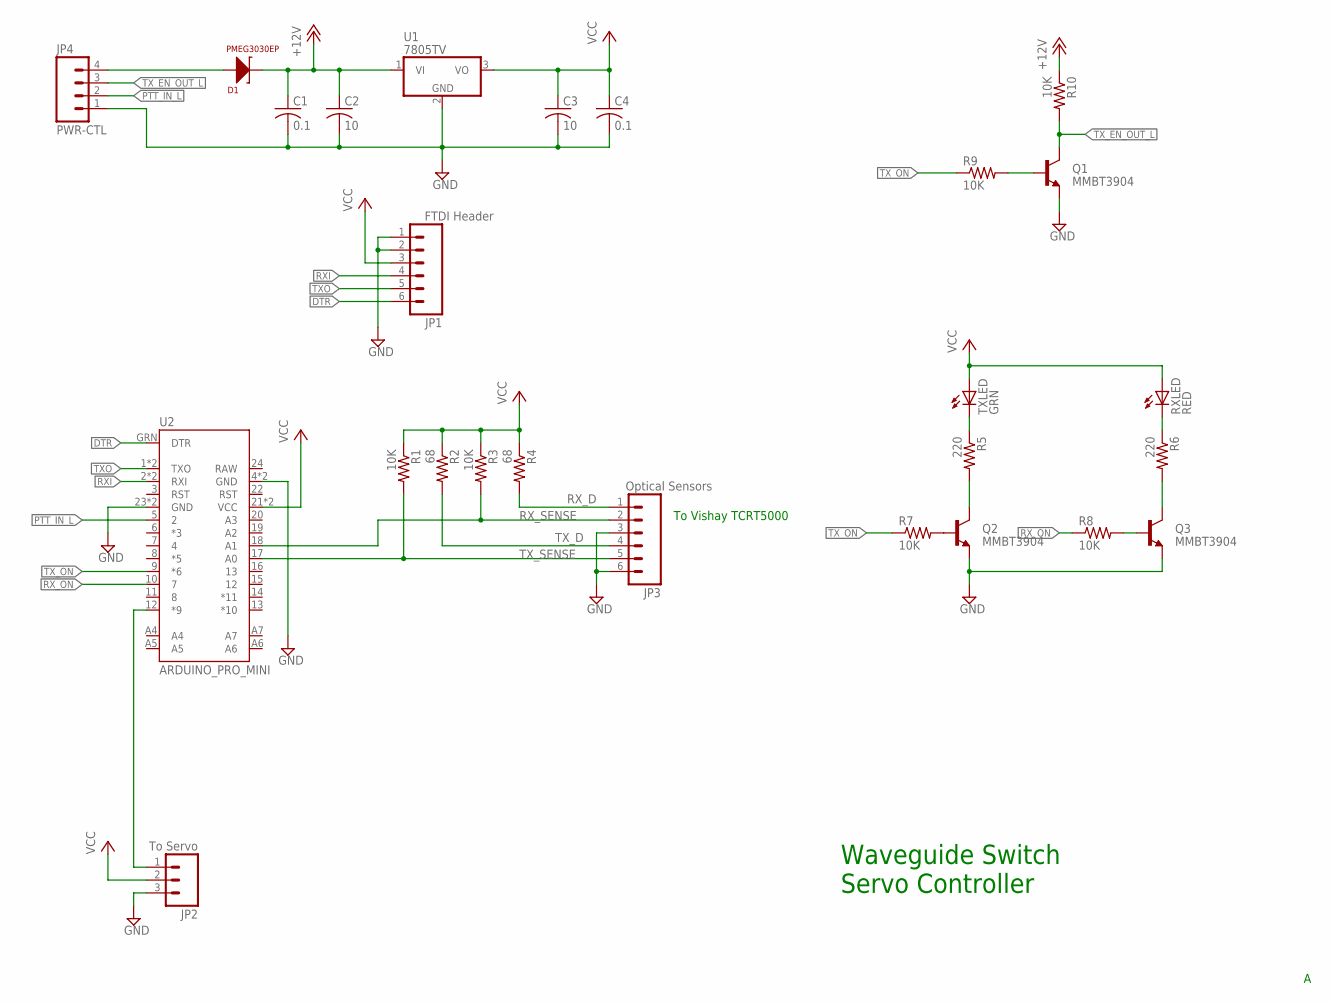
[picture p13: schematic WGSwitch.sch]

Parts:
C1, C4: 0.1; C0805K
C2, C3: 10; C1206K
D1: PMEG3030EP; SOD128
JP1: FTDI Header; 1X06
JP2: To Servo; 1X03
JP3: Optical Sensors; 1X06
JP4: PWR-CTL; 1X04
Q1, Q2, Q3: MMBT3904; SOT23-3
R1, R3, R7, R8, R9, R10: 10K; R1206
R2, R4: 68; R1206
R5, R6: 220; R1206
RXLED: RED; LED5MM
TXLED: GRN; LED5MM
U1: 7805TV; TO220V
U2: ARDUINO_PRO_MINI

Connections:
+12V: C1.1, C2.1, D1.P$2 (C), R10.1, U1.1 (VI)
DTR: JP1.6, U2.GRN (DTR)
GND: C1.2, C2.2, C3.2, C4.2, JP1.1, JP1.2, JP2.3, JP3.3, JP3.6, JP4.1, Q1.2 (E), Q2.2 (E), Q3.2 (E), U1.2 (GND), U2.4 (GND), U2.23 (GND), U2.BLK (GND), U2.GND
unnamed: JP2.1, U2.12 (*9)
unnamed: Q1.1 (B), R9.2
unnamed: Q2.1 (B), R7.2
unnamed: R6.1, RXLED.K (C)
unnamed: Q2.3 (C), R5.2
unnamed: Q3.3 (C), R6.2
unnamed: Q3.1 (B), R8.2
unnamed: D1.P$1 (A), JP4.4
PTT_IN_L: JP4.2, U2.5 (2)
RXI: JP1.4, U2.2 (RXI), U2.RXI
RX_D: JP3.1, R4.2
RX_ON: R8.1, U2.10 (7)
RX_SENSE: JP3.2, R3.2, U2.18 (A1)
TXO: JP1.5, U2.1 (TXO), U2.TXO
TX_D: JP3.4, R2.2
TX_EN_OUT_L: JP4.3, Q1.3 (C), R10.2
TX_LED: R5.1, TXLED.K (C)
TX_ON: R7.1, R9.1, U2.9 (*6)
TX_SENSE: JP3.5, R1.2, U2.17 (A0)
VCC: C3.1, C4.1, JP1.3, JP2.2, R1.1, R2.1, R3.1, R4.1, RXLED.A, TXLED.A, U1.3 (VO), U2.21 (VCC), U2.VCC

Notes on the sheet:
To Vishay TCRT5000
Waveguide Switch Servo Controller

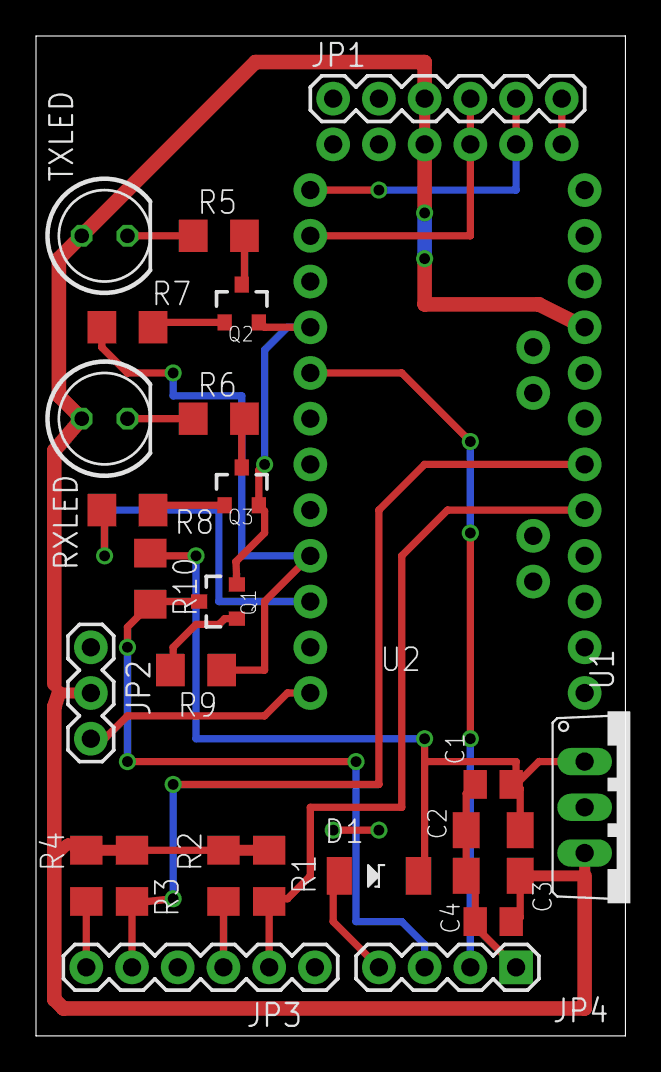
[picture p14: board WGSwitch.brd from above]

Board: 2 copper layers, 32.7 x 55.5 mm, 26 parts (0 on the bottom side), 23 nets.

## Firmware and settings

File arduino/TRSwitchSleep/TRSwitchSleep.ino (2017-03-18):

/*
Copyright (c) 2016, Matthew H. Reilly (kb1vc)
All rights reserved.

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
*/
#include <Servo.h> 
#include <avr/interrupt.h>
#include <avr/sleep.h>
 
Servo myservo;  // create servo object to control a servo 
 
int RX_pos = 0;
int RX_rest_pos = 90;
int TX_pos = 175;
int TX_rest_pos = 90;
int Center = 90;
int actuator_delay = 750; // in mS

#define SERVO_PIN 9
#define SENSE_PIN 2
#define OUT_PIN 3
#define RX_LED 7
#define TX_LED 6
#define RX_Sense A1
#define TX_Sense A0

#define RX_Threshold 250
#define TX_Threshold 250

volatile int PTT_interrupt_occurred;
volatile int PTT_pin_state;

#define RX_MODE 1
#define TX_MODE -1
#define NO_MODE 0

void setup() 
{ 
  myservo.attach(SERVO_PIN);  // attaches the servo on pin 9 to the servo object 
  pinMode(SENSE_PIN, INPUT_PULLUP);
  pinMode(OUT_PIN, OUTPUT);
  pinMode(RX_LED, OUTPUT);
  pinMode(TX_LED, OUTPUT);
  delay(500);
  setMode(1);

  PTT_pin_state = 1;   
} 

void goto_sleep()
{
  set_sleep_mode(SLEEP_MODE_PWR_DOWN);
  noInterrupts(); // hold off interrupts while we're sleeping
  sleep_enable();
  attachInterrupt(digitalPinToInterrupt(SENSE_PIN), PTT_isr, CHANGE);
  interrupts();
  sleep_cpu(); // goto sleep.
}

void PTT_isr()
{
  sleep_disable();   // don't go back to sleep until we've got the interrupt handled. (prevents a race between sleep_enable and attach)
  detachInterrupt(digitalPinToInterrupt(SENSE_PIN)); 
  PTT_interrupt_occurred = 1;
  PTT_pin_state = digitalRead(SENSE_PIN);
}

// return 1 for RX -1 for TX and 0 for no dice
int checkSensors()
{
  int rxs = analogRead(RX_Sense);
  int txs = analogRead(TX_Sense);
  
  if((rxs < RX_Threshold) && (txs > TX_Threshold)) 
    return 1;
  else if((rxs > RX_Threshold) && (txs < TX_Threshold))
    return -1;
  else {

    return 0;
  }
}

void setLEDs(int mode)
{
  if(mode == RX_MODE) {
    digitalWrite(RX_LED, HIGH);
    digitalWrite(TX_LED, LOW);
  }
  else if(mode == TX_MODE) {
    digitalWrite(RX_LED, LOW);
    digitalWrite(TX_LED, HIGH);
  }
  else {
    digitalWrite(RX_LED, LOW);
    digitalWrite(TX_LED, LOW);
  }
}
 
void setMode(int mode) {
  int flag = 1; 
  int count = 0;

  setLEDs(NO_MODE); 
  if(mode == RX_MODE) {
    myservo.write(RX_pos);
    while(flag) {
      checkSensors();  // read twice to spin up A/D converter
      if(checkSensors() == 1) flag = 0;
      else {
        count++; 
        if(count == 100) {
          myservo.write(RX_pos);
          count = 0;
        } 
      }
    }
    myservo.write(RX_rest_pos);
    setLEDs(RX_MODE);
  }
  else if (mode == TX_MODE) {
    myservo.write(TX_pos);
    while(flag) {
      checkSensors(); // read twice to spin up A/D converter
      if(checkSensors() == -1) flag = 0;
      else {
        count++;
        if(count == 100) {
          myservo.write(TX_pos);
          count = 0; 
        }
      }
    }
    myservo.write(TX_rest_pos);   
    setLEDs(TX_MODE);
  }
}

void loop() 
{ 
  // pin state is low for TX.
  if(PTT_pin_state) {
    setMode(RX_MODE);
  }
  else {
    setMode(TX_MODE);
  }
  delay(actuator_delay);
  goto_sleep();
} 

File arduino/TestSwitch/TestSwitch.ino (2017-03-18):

#define SENSE_PIN 2
#define PTT_PIN 9

void setup() {
  // put your setup code here, to run once:
   pinMode(SENSE_PIN, INPUT);
   pinMode(PTT_PIN, OUTPUT);
   
   Serial.begin(19200);
   while(!Serial);
}

void loop() {
  // put your main code here, to run repeatedly:
  int sense; 
  unsigned long tst, ten, dur; 
  
  while(1) {
    sense=0;

    digitalWrite(PTT_PIN, LOW);
    tst = millis();   
    while(!sense) {
        sense = digitalRead(SENSE_PIN);
        ten = millis();
    }
    dur = ten - tst; 
    Serial.print(dur); Serial.print(" wrote low  got "); Serial.println(sense);
    delay(1000);
    
    sense=1;
    digitalWrite(PTT_PIN, HIGH); 
    tst = millis();   
    while(sense) {
        sense = digitalRead(SENSE_PIN);
        ten = millis();
    }
    dur = ten - tst; 
    Serial.print(dur); Serial.print(" wrote high  got "); Serial.println(sense);    

    delay(1000);
  }
}

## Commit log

2017-01-19 Almost there.
    [WGSwitch.scad]
2017-01-21 New trial -- reduce slug height
    [WGSwitch.scad]
2017-01-21 Final proto?
    [WGSwitch.scad]
2017-01-28 Made cover... adjusted base.
    [WGSwitch.scad]
2017-02-20 Added controller sketch, and new PC module.
    [WGSwitch.brd, WGSwitch.scad, WGSwitch.sch]
2017-02-21 Added optical sensors. Trimmed slug to fit them.
    [WGSwitch.scad]
2017-02-22 Added hole and tabs for connector mount
    [WGSwitch.scad]
2017-02-23 Added mount for connector.
    [TCRT5000_Mount.scad]
2017-02-23 added picture of trial and error.
    [WGSwitch.scad]
2017-03-05 update sketch to work with full module.
    [WGSwitch.scad]
2017-03-11 Added Sleep Mode version
    [WGSwitch.scad]
2017-03-11 Bumped IR sensor thresholds to handle dark envelope.
2017-03-11 cleanup and optimize TRSwitchSleep to eliminate extra delay.
    [WGSwitch.brd, WGSwitch.sch]
2017-03-15 more progress -- added images
    [HP6289_inner.scad]
2017-03-18 Just about right.
    [ExplodedView.scad, WGSwitch.brd, WGSwitch.sch]
2017-04-15 Saving the module... this will be rev B.
    [WGSwitchController.kicad_pcb, WGSwitchController.sch]
2017-04-15 Rev C of module -- fixed diode footprints.
    [WGSwitchController.kicad_pcb, WGSwitchController.sch]

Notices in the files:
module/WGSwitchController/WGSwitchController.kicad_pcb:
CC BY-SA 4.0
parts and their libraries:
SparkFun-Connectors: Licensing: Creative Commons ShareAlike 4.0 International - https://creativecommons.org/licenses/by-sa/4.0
